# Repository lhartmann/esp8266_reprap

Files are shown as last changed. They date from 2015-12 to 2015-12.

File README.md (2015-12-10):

#ESP8266 I2S 32bit Realtime Shift Register Driver 

I believe I found a way to use just an ESP8266 module to control a set of 3D printer stepper drivers directly. This code demonstrates how.

Background:

1.  Other projects show how to use ESP01 as a wifi-serial bridge to the arduinos, but serial is still a bottleneck and wifi uploads are impractical.
2.  Altough ESP8266 does 160MHz at 32bits processing (versus 16MHZ 8-bit from most Arduinos) it has insufficient realtime GPIO for controlling printers.
3.  Raspberry pi shared the realtime gpio limitation, but wallacoloo still did reprap control using DMA. Nice! https://www.youtube.com/watch?v=g4UD5MRas3E
4.  CNLohr did a really cool WS2812 led driver (weird one-wire serial protocol) using ESP8266 I2S audio output and DMA. https://www.youtube.com/watch?v=6zqGwxqJQnw
5.  I2S and SPI look very much alike, and SPI can control shift registers. Hey! Opportunity!

I got the code from CNLohr on github, modified it to output a 32 bit counter (16 bit left + 16 bit right channels) via a circular DMA buffer, and created a small PCB with four cascaded 74HC595 shift registers. wiring is simple:
- I2S Data to '595 input data
- I2S Bitclock to '595 shift clock
- I2s word clock (left/right) to '595 buffer clock.

This is what RAW I2S output signals for the counter look like: word-clock (yellow), bit clock (cyan), data (purple). Notice how LSB of data is output after the word clock rising edge.

IMAGE ALT TEXT HERE (http://www.youtube.com/watch?v=Fhat7x_vPLw)

Fixed the offset (software shifing) to match the parallel outputs, raised the frequency a bit (just cause), plugged in the shifter board. Now this is what word-clock (yellow) and the 3LSBs (cyan=1, purple=2, blue=4) look like:
image of osciloscope

The code and the PCB: (https://github.com/lhartmann/esp8266_reprap)

What this does:

- Allows realtime bitbanging of 32 data bits via I2S and DMA.
- Demo code just outputs a 32bit counter at 185kHz sample rate.
- Reference shifter board is provided.

Limitations:

- 1MSB is actually delayed by 1 sample due to I2S signaling standard. This delay is constant so it could be compensated, but I didn't bother.

Hopes for the future: RepRap 3D Printing.

- No extra arduino necessary, ESP would control the drivers directly.
- SDcard uploads over wifi would be feasible for large files, no more serial connection bottleneck with wifi-serial bridging. 
- Browser-side slicing with slic3r and (http://www.skulpt.org). No software install required on the client!

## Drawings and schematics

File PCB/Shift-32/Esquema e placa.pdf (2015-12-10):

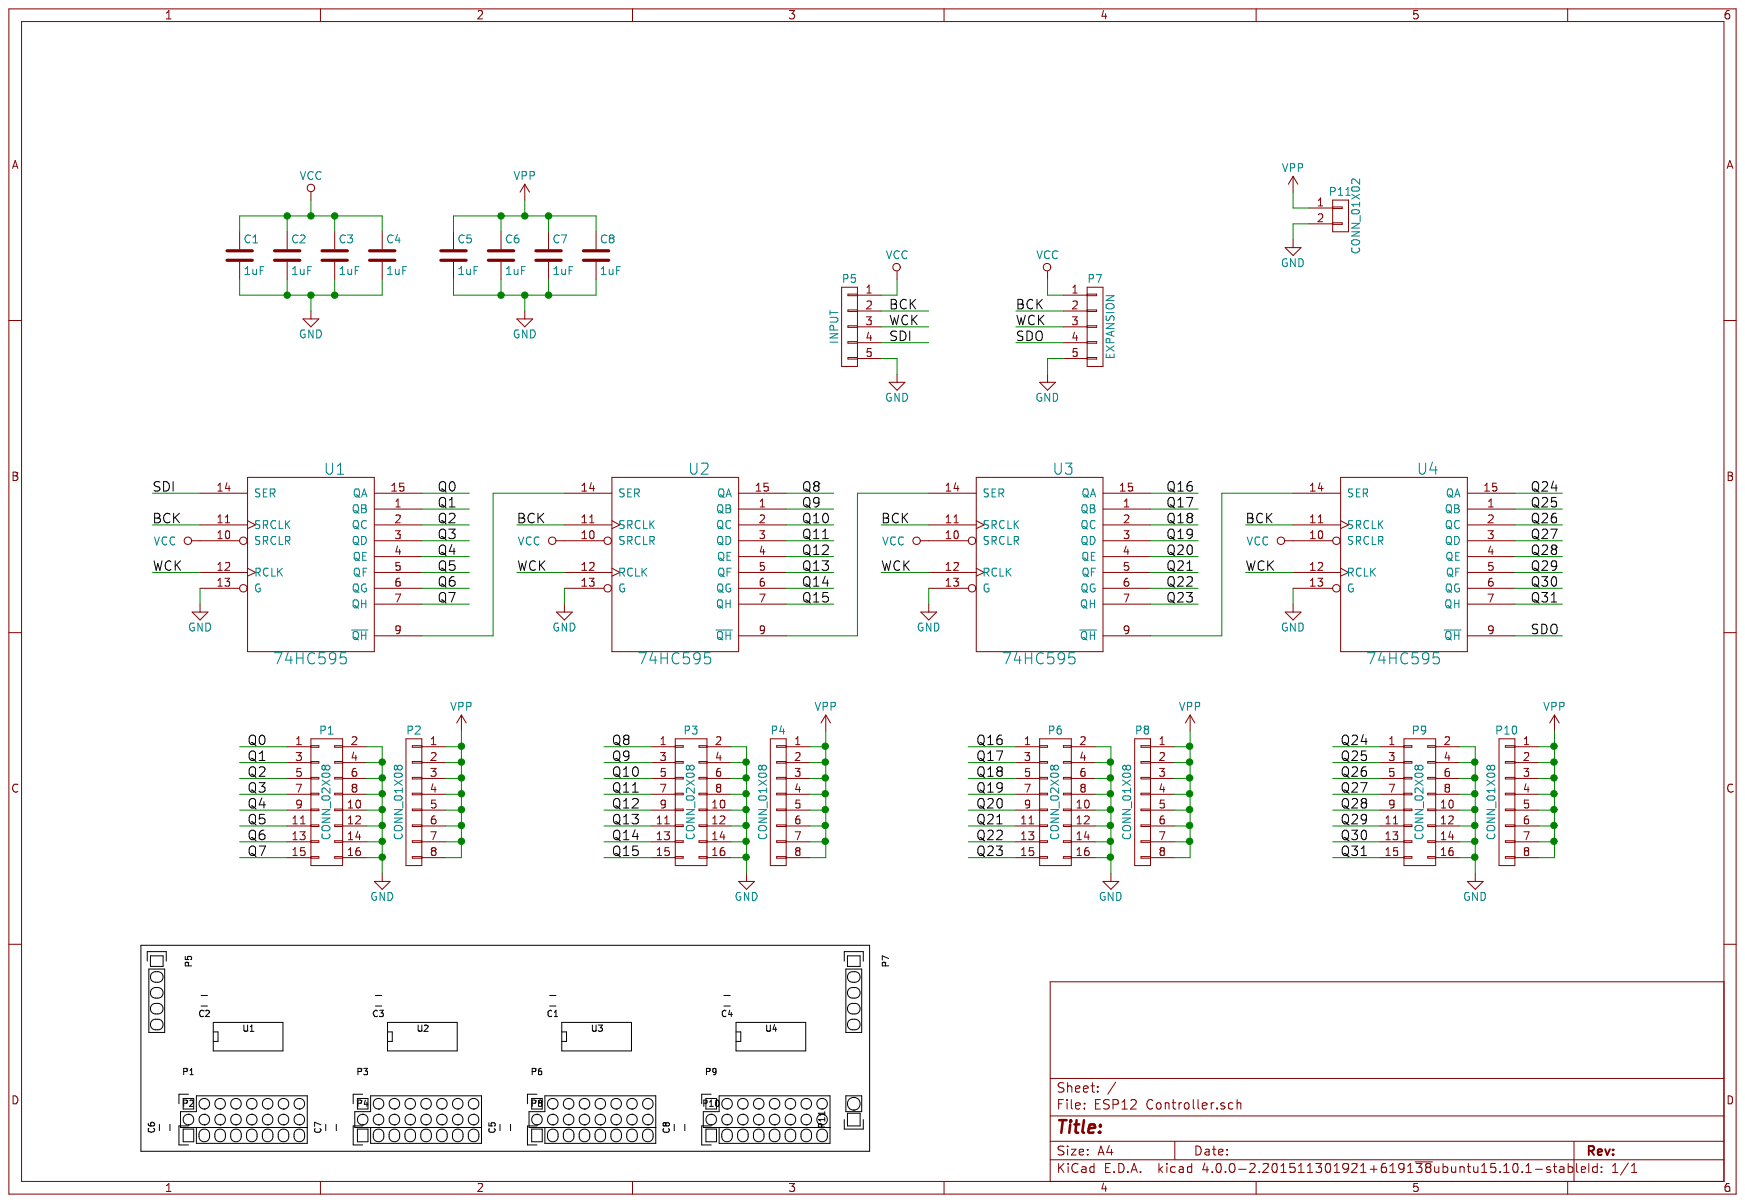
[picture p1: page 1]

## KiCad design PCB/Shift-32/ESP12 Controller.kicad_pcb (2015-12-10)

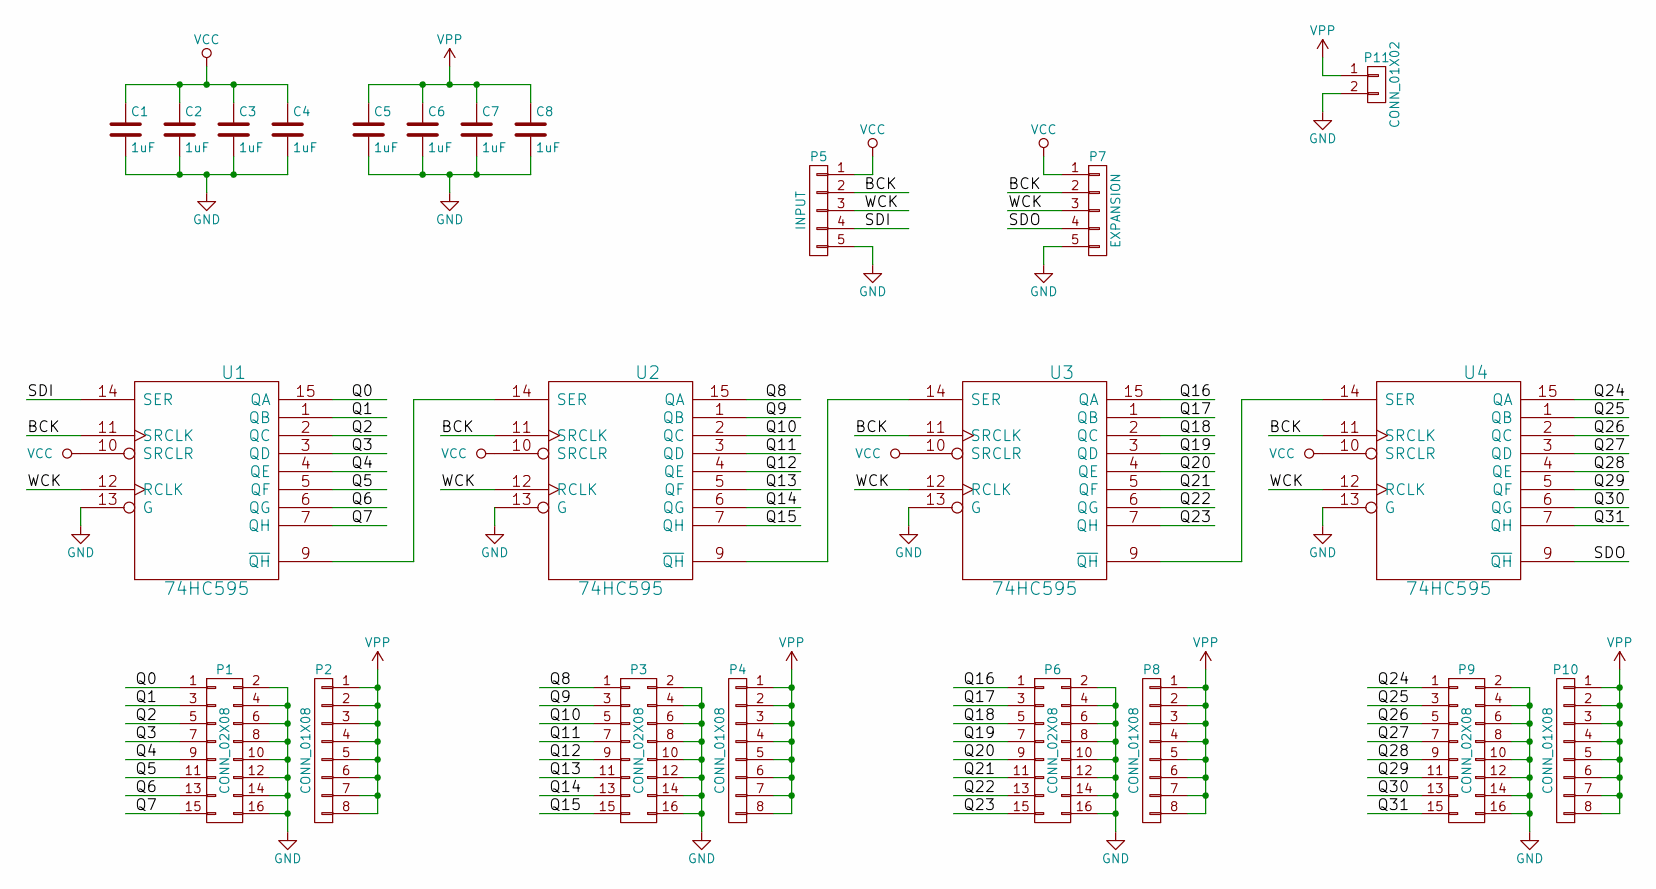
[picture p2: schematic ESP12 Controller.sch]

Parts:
C1, C2, C3, C4, C5, C6, C7, C8: 1uF; C_0805_HandSoldering
P1, P3, P6, P9: CONN_02X08; Socket_Strip_Straight_2x08
P2, P4, P8, P10: CONN_01X08; Socket_Strip_Straight_1x08
P5: INPUT; Socket_Strip_Straight_1x05
P7: EXPANSION; Socket_Strip_Straight_1x05
P11: CONN_01X02; Socket_Strip_Straight_1x02
U1, U2, U3, U4: 74HC595; SO-16-N

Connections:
/BCK: P5.2, P7.2, U1.11 (SRCLK), U2.11 (SRCLK), U3.11 (SRCLK), U4.11 (SRCLK)
/Q0: P1.1, U1.15 (QA)
/Q1: P1.3, U1.1 (QB)
/Q2: P1.5, U1.2 (QC)
/Q3: P1.7, U1.3 (QD)
/Q4: P1.9, U1.4 (QE)
/Q5: P1.11, U1.5 (QF)
/Q6: P1.13, U1.6 (QG)
/Q7: P1.15, U1.7 (QH)
/Q8: P3.1, U2.15 (QA)
/Q9: P3.3, U2.1 (QB)
/Q10: P3.5, U2.2 (QC)
/Q11: P3.7, U2.3 (QD)
/Q12: P3.9, U2.4 (QE)
/Q13: P3.11, U2.5 (QF)
/Q14: P3.13, U2.6 (QG)
/Q15: P3.15, U2.7 (QH)
/Q16: P6.1, U3.15 (QA)
/Q17: P6.3, U3.1 (QB)
/Q18: P6.5, U3.2 (QC)
/Q19: P6.7, U3.3 (QD)
/Q20: P6.9, U3.4 (QE)
/Q21: P6.11, U3.5 (QF)
/Q22: P6.13, U3.6 (QG)
/Q23: P6.15, U3.7 (QH)
/Q24: P9.1, U4.15 (QA)
/Q25: P9.3, U4.1 (QB)
/Q26: P9.5, U4.2 (QC)
/Q27: P9.7, U4.3 (QD)
/Q28: P9.9, U4.4 (QE)
/Q29: P9.11, U4.5 (QF)
/Q30: P9.13, U4.6 (QG)
/Q31: P9.15, U4.7 (QH)
/SDI: P5.4, U1.14 (SER)
/SDO: P7.4, U4.9 (~QH)
/WCK: P5.3, P7.3, U1.12 (RCLK), U2.12 (RCLK), U3.12 (RCLK), U4.12 (RCLK)
GND: C1.2, C2.2, C3.2, C4.2, C5.2, C6.2, C7.2, C8.2, P1.2, P1.4, P1.6, P1.8, P1.10, P1.12, P1.14, P1.16, P3.2, P3.4, P3.6, P3.8, P3.10, P3.12, P3.14, P3.16, P5.5, P6.2, P6.4, P6.6, P6.8, P6.10, P6.12, P6.14, P6.16, P7.5, P9.2, P9.4, P9.6, P9.8, P9.10, P9.12, P9.14, P9.16, P11.2, U1.8 (GND), U1.13 (G), U2.8 (GND), U2.13 (G), U3.8 (GND), U3.13 (G), U4.8 (GND), U4.13 (G)
unnamed: U1.9 (~QH), U2.14 (SER)
unnamed: U2.9 (~QH), U3.14 (SER)
unnamed: U3.9 (~QH), U4.14 (SER)
VCC: C1.1, C2.1, C3.1, C4.1, P5.1, P7.1, U1.10 (SRCLR), U1.16 (VCC), U2.10 (SRCLR), U2.16 (VCC), U3.10 (SRCLR), U3.16 (VCC), U4.10 (SRCLR), U4.16 (VCC)
VPP: C5.1, C6.1, C7.1, C8.1, P2.1, P2.2, P2.3, P2.4, P2.5, P2.6, P2.7, P2.8, P4.1, P4.2, P4.3, P4.4, P4.5, P4.6, P4.7, P4.8, P8.1, P8.2, P8.3, P8.4, P8.5, P8.6, P8.7, P8.8, P10.1, P10.2, P10.3, P10.4, P10.5, P10.6, P10.7, P10.8, P11.1

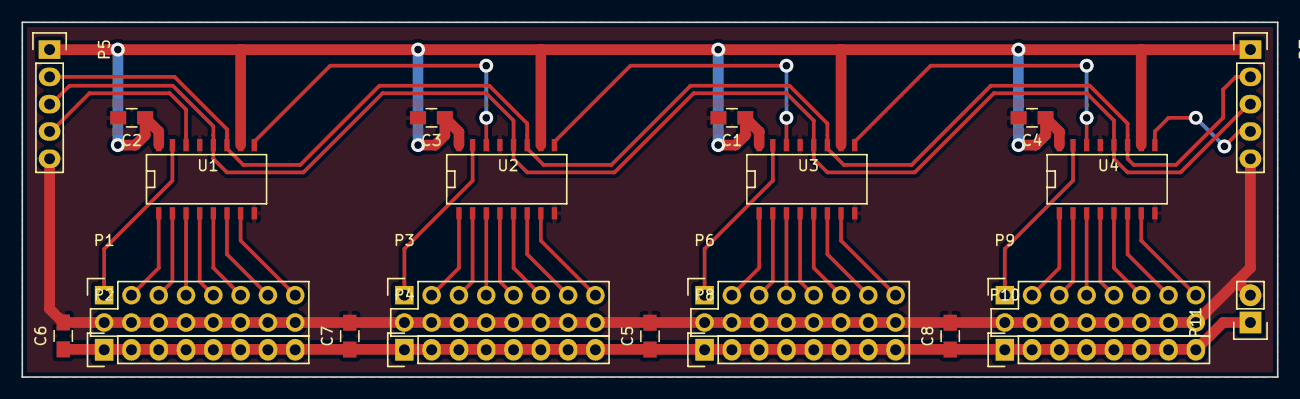
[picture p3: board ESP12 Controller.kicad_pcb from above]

Board: 2 copper layers, 116.8 x 33.0 mm, 23 parts (0 on the bottom side), 42 nets.

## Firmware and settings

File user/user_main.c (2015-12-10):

//Copyright 2015 <>< Charles Lohr, see LICENSE file.

#include "mem.h"
#include "c_types.h"
#include "user_interface.h"
#include "ets_sys.h"
#include "driver/uart.h"
#include "osapi.h"
#include "espconn.h"
#include "mystuff.h"
#include "ws2812_i2s.h"
#include "commonservices.h"
#include <mdns.h>

#define PORT 7777

#define procTaskPrio        0
#define procTaskQueueLen    1

static volatile os_timer_t some_timer;
static struct espconn *pUdpServer;
uint8_t last_leds[512*3];
int last_led_count;


//int ICACHE_FLASH_ATTR StartMDNS();

void user_rf_pre_init(void)
{
	//nothing.
}


char * strcat( char * dest, char * src )
{
	return strcat(dest, src );
}



//Tasks that happen all the time.

os_event_t    procTaskQueue[procTaskQueueLen];

static void ICACHE_FLASH_ATTR procTask(os_event_t *events)
{
	CSTick( 0 );
	system_os_post(procTaskPrio, 0, 0 );
}

//Timer event.
static void ICACHE_FLASH_ATTR myTimer(void *arg)
{
	CSTick( 1 );
}


//Called when new packet comes in.
static void ICACHE_FLASH_ATTR
udpserver_recv(void *arg, char *pusrdata, unsigned short len)
{
	struct espconn *pespconn = (struct espconn *)arg;

	uart0_sendStr("X");


	len -= 3;
	if( len > sizeof(last_leds) + 3 )
	{
		len = sizeof(last_leds) + 3;
	}
	ets_memcpy( last_leds, pusrdata+3, len );
	last_led_count = len / 3;
}

void ICACHE_FLASH_ATTR charrx( uint8_t c )
{
	//Called from UART.
}

void user_init(void)
{
	uart_init(BIT_RATE_115200, BIT_RATE_115200);

	uart0_sendStr("\r\nesp8266 ws2812 driver\r\n");

//	int opm = wifi_get_opmode();
//	if( opm == 1 ) need_to_switch_opmode = 120;
//	wifi_set_opmode_current(2);
//Uncomment this to force a system restore.
//	system_restore();

	CSSettingsLoad( 0 );
	CSPreInit();

    pUdpServer = (struct espconn *)os_zalloc(sizeof(struct espconn));
	ets_memset( pUdpServer, 0, sizeof( struct espconn ) );
	espconn_create( pUdpServer );
	pUdpServer->type = ESPCONN_UDP;
	pUdpServer->proto.udp = (esp_udp *)os_zalloc(sizeof(esp_udp));
	pUdpServer->proto.udp->local_port = 7777;
	espconn_regist_recvcb(pUdpServer, udpserver_recv);

	if( espconn_create( pUdpServer ) )
	{
		while(1) { uart0_sendStr( "\r\nFAULT\r\n" ); }
	}

	CSInit();

	SetServiceName( "ws2812" );
	AddMDNSName( "cn8266" );
	AddMDNSName( "ws2812" );
	AddMDNSService( "_http._tcp", "An ESP8266 Webserver", 80 );
	AddMDNSService( "_ws2812._udp", "WS2812 Driver", 7777 );
	AddMDNSService( "_cn8266._udp", "ESP8266 Backend", 7878 );

	//Add a process
	system_os_task(procTask, procTaskPrio, procTaskQueue, procTaskQueueLen);

	//Timer example
	os_timer_disarm(&some_timer);
	os_timer_setfn(&some_timer, (os_timer_func_t *)myTimer, NULL);
	os_timer_arm(&some_timer, 100, 1);

	reprap_dmaio_init();

	system_os_post(procTaskPrio, 0, 0 );
}


//There is no code in this project that will cause reboots if interrupts are disabled.
void EnterCritical()
{
}

void ExitCritical()
{
}

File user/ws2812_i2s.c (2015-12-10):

/******************************************************************************
 * Copyright 2013-2015 Espressif Systems
 *           2015 <>< Charles Lohr
 *
 * FileName: i2s_freertos.c
 *
 * Description: I2S output routines for a FreeRTOS system. Uses DMA and a queue
 * to abstract away the nitty-gritty details.
 *
 * Modification history:
 *     2015/06/01, v1.0 File created.
 *     2015/07/23, Switch to making it a WS2812 output device.
*******************************************************************************

Notes:

 This is pretty badly hacked together from the MP3 example.
 I spent some time trying to strip it down to avoid a lot of the TX_ stuff. 
 That seems to work.

 Major suggestions that I couldn't figure out:
	* Use interrupts to disable DMA, so it isn't running nonstop.
    * Use interrupts to flag when new data can be sent.

 When I try using interrupts, it seems to work for a bit but things fall apart
 rather quickly and the engine just refuses to send anymore until reboot.

 The way it works right now is to keep the DMA running forever and just update
 the data in the buffer so it continues sending the frame.

Extra copyright info:
  Actually not much of this file is Copyright Espressif, comparativly little
  mostly just the stuff to make the I2S bus go.

*******************************************************************************/


#include "slc_register.h"
#include "mystuff.h"
#include <c_types.h>
#include "ws2812_i2s.h"
#include "user_interface.h"
#include "pin_mux_register.h"

//Creates an I2S SR of 93,750 Hz, or 3 MHz Bitclock (.333us/sample)
// 12000000L/(div*bestbck*2)
//It is likely you could speed this up a little.

#define WS_I2S_BCK 10  //Seems to work as low as 14, shoddy at 13.
#define WS_I2S_DIV 4

#ifndef i2c_bbpll
#define i2c_bbpll                                 0x67
#define i2c_bbpll_en_audio_clock_out            4
#define i2c_bbpll_en_audio_clock_out_msb        7
#define i2c_bbpll_en_audio_clock_out_lsb        7
#define i2c_bbpll_hostid                           4

#define i2c_writeReg_Mask(block, host_id, reg_add, Msb, Lsb, indata)  rom_i2c_writeReg_Mask(block, host_id, reg_add, Msb, Lsb, indata)
#define i2c_readReg_Mask(block, host_id, reg_add, Msb, Lsb)  rom_i2c_readReg_Mask(block, host_id, reg_add, Msb, Lsb)
#define i2c_writeReg_Mask_def(block, reg_add, indata) \
      i2c_writeReg_Mask(block, block##_hostid,  reg_add,  reg_add##_msb,  reg_add##_lsb,  indata)
#define i2c_readReg_Mask_def(block, reg_add) \
      i2c_readReg_Mask(block, block##_hostid,  reg_add,  reg_add##_msb,  reg_add##_lsb)
#endif
#ifndef ETS_SLC_INUM
#define ETS_SLC_INUM       1
#endif



//From i2s_reg.h
#define DR_REG_I2S_BASE (0x60000e00)

#define I2STXFIFO  (DR_REG_I2S_BASE + 0x0000)
#define I2SRXFIFO  (DR_REG_I2S_BASE + 0x0004)
#define I2SCONF  (DR_REG_I2S_BASE + 0x0008)
#define I2S_BCK_DIV_NUM 0x0000003F
#define I2S_BCK_DIV_NUM_S 22
#define I2S_CLKM_DIV_NUM 0x0000003F
#define I2S_CLKM_DIV_NUM_S 16
#define I2S_BITS_MOD 0x0000000F
#define I2S_BITS_MOD_S 12
#define I2S_RECE_MSB_SHIFT (BIT(11))
#define I2S_TRANS_MSB_SHIFT (BIT(10))
#define I2S_I2S_RX_START (BIT(9))
#define I2S_I2S_TX_START (BIT(8))
#define I2S_MSB_RIGHT (BIT(7))
#define I2S_RIGHT_FIRST (BIT(6))
#define I2S_RECE_SLAVE_MOD (BIT(5))
#define I2S_TRANS_SLAVE_MOD (BIT(4))
#define I2S_I2S_RX_FIFO_RESET (BIT(3))
#define I2S_I2S_TX_FIFO_RESET (BIT(2))
#define I2S_I2S_RX_RESET (BIT(1))
#define I2S_I2S_TX_RESET (BIT(0))
#define I2S_I2S_RESET_MASK 0xf

 #define I2SINT_RAW (DR_REG_I2S_BASE + 0x000c)
#define I2S_I2S_TX_REMPTY_INT_RAW (BIT(5))
#define I2S_I2S_TX_WFULL_INT_RAW (BIT(4))
#define I2S_I2S_RX_REMPTY_INT_RAW (BIT(3))
#define I2S_I2S_RX_WFULL_INT_RAW (BIT(2))
#define I2S_I2S_TX_PUT_DATA_INT_RAW (BIT(1))
#define I2S_I2S_RX_TAKE_DATA_INT_RAW (BIT(0))


#define I2SINT_ST (DR_REG_I2S_BASE + 0x0010)
#define I2S_I2S_TX_REMPTY_INT_ST (BIT(5))
#define I2S_I2S_TX_WFULL_INT_ST (BIT(4))
#define I2S_I2S_RX_REMPTY_INT_ST (BIT(3))
#define I2S_I2S_RX_WFULL_INT_ST (BIT(2))
#define I2S_I2S_TX_PUT_DATA_INT_ST (BIT(1))
#define I2S_I2S_RX_TAKE_DATA_INT_ST (BIT(0))

 #define I2SINT_ENA (DR_REG_I2S_BASE + 0x0014)
#define I2S_I2S_TX_REMPTY_INT_ENA (BIT(5))
#define I2S_I2S_TX_WFULL_INT_ENA (BIT(4))
#define I2S_I2S_RX_REMPTY_INT_ENA (BIT(3))
#define I2S_I2S_RX_WFULL_INT_ENA (BIT(2))
#define I2S_I2S_TX_PUT_DATA_INT_ENA (BIT(1))
#define I2S_I2S_RX_TAKE_DATA_INT_ENA (BIT(0))

 #define I2SINT_CLR (DR_REG_I2S_BASE + 0x0018)
#define I2S_I2S_TX_REMPTY_INT_CLR (BIT(5))
#define I2S_I2S_TX_WFULL_INT_CLR (BIT(4))
#define I2S_I2S_RX_REMPTY_INT_CLR (BIT(3))
#define I2S_I2S_RX_WFULL_INT_CLR (BIT(2))
#define I2S_I2S_PUT_DATA_INT_CLR (BIT(1))
#define I2S_I2S_TAKE_DATA_INT_CLR (BIT(0))

#define I2STIMING (DR_REG_I2S_BASE + 0x001c)
#define I2S_TRANS_BCK_IN_INV (BIT(22))
#define I2S_RECE_DSYNC_SW (BIT(21))
#define I2S_TRANS_DSYNC_SW (BIT(20))
#define I2S_RECE_BCK_OUT_DELAY 0x00000003
#define I2S_RECE_BCK_OUT_DELAY_S 18
#define I2S_RECE_WS_OUT_DELAY 0x00000003
#define I2S_RECE_WS_OUT_DELAY_S 16
#define I2S_TRANS_SD_OUT_DELAY 0x00000003
#define I2S_TRANS_SD_OUT_DELAY_S 14
#define I2S_TRANS_WS_OUT_DELAY 0x00000003
#define I2S_TRANS_WS_OUT_DELAY_S 12
#define I2S_TRANS_BCK_OUT_DELAY 0x00000003
#define I2S_TRANS_BCK_OUT_DELAY_S 10
#define I2S_RECE_SD_IN_DELAY 0x00000003
#define I2S_RECE_SD_IN_DELAY_S 8
#define I2S_RECE_WS_IN_DELAY 0x00000003
#define I2S_RECE_WS_IN_DELAY_S 6
#define I2S_RECE_BCK_IN_DELAY 0x00000003
#define I2S_RECE_BCK_IN_DELAY_S 4
#define I2S_TRANS_WS_IN_DELAY 0x00000003
#define I2S_TRANS_WS_IN_DELAY_S 2
#define I2S_TRANS_BCK_IN_DELAY 0x00000003
#define I2S_TRANS_BCK_IN_DELAY_S 0

#define I2S_FIFO_CONF (DR_REG_I2S_BASE + 0x0020)
#define I2S_I2S_RX_FIFO_MOD 0x00000007
#define I2S_I2S_RX_FIFO_MOD_S 16
#define I2S_I2S_TX_FIFO_MOD 0x00000007
#define I2S_I2S_TX_FIFO_MOD_S 13
#define I2S_I2S_DSCR_EN (BIT(12))
#define I2S_I2S_TX_DATA_NUM 0x0000003F
#define I2S_I2S_TX_DATA_NUM_S 6
#define I2S_I2S_RX_DATA_NUM 0x0000003F
#define I2S_I2S_RX_DATA_NUM_S 0


#define I2SRXEOF_NUM (DR_REG_I2S_BASE + 0x0024)
#define I2S_I2S_RX_EOF_NUM 0xFFFFFFFF
#define I2S_I2S_RX_EOF_NUM_S 0

#define I2SCONF_SIGLE_DATA (DR_REG_I2S_BASE + 0x0028)
#define I2S_I2S_SIGLE_DATA 0xFFFFFFFF
#define I2S_I2S_SIGLE_DATA_S 0

#define I2SCONF_CHAN (DR_REG_I2S_BASE + 0x002c)
#define I2S_RX_CHAN_MOD 0x00000003
#define I2S_RX_CHAN_MOD_S 3
#define I2S_TX_CHAN_MOD 0x00000007
#define I2S_TX_CHAN_MOD_S 0

//From sdio_slv.h

struct sdio_queue
{
	uint32	blocksize:12;
	uint32	datalen:12;
	uint32	unused:5;
	uint32	sub_sof:1;
	uint32 	eof:1;
	uint32	owner:1;

	uint32	buf_ptr;
	uint32	next_link_ptr;
};

struct sdio_slave_status_element
{
	uint32 wr_busy:1;
	uint32 rd_empty :1;
	uint32 comm_cnt :3;
	uint32 intr_no :3;
	uint32 rx_length:16;
	uint32 res:8;
};

union sdio_slave_status
{
	struct sdio_slave_status_element elm_value;
	uint32 word_value;
};

#define RX_AVAILIBLE 2
#define TX_AVAILIBLE 1
#define INIT_STAGE	 0
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
